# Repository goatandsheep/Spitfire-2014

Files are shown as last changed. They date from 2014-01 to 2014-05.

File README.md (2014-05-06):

McMaster Solar Car Club
=======================

Welcome to McMaster University's Solar Car Club's GitHub Repository. This is where we will keep all of our project files. We are currently in the process of transferring files from the Dropbox folder to here.

This is the link to the Solar Car Room Drawer Inventory: http://goo.gl/nMddYb

This is the link to the main Solar Car website: http://www.macsolarcar.com/

If you are new to GitHub, don't fret-we have included a tutorial on how to use it: http://goo.gl/4RcD2u

Note: [.md](https://en.wikipedia.org/wiki/Markdown) files can be opened like .txt files, but look cool up on GitHub

Target Release date: End of February, 2014

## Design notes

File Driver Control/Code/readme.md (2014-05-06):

TRI86 EV driver controls MSP430 firmware README
================================================

* This firmware is written to use the GNU GCC3 toolchain, please read the install instructions below.
* Refer to the board schematics, available on the Tritium website, for pinouts and device functionality.
* The firmware is licenced using the BSD licence.  There is no obligation to publish modifications.
* If you've written something cool and would like to share, please let us know about it!
* Contact James Kennedy with any questions or comments: [james@tritium.com.au](mailto:james@tritium.com.au)

Toolchain walkthrough (Windows MSPGCC instructions)
---------------------------------------------------

1. Download and [install the 2008-12-30 release of MSPGCC3](
  http://sourceforge.net/projects/mspgcc/files/Outdated/mspgcc-win32/snapshots/mspgcc-20081230.exe/download)
  The Tritium bootloader tool requires this specific version of GCC, as it has not yet been updated to use the
  output from the current GCC4 tools.

2. Download and install the [current MinGW](http://sourceforge.net/projects/mingw/files/), and use the install options for the C compliler + MSYS. This gets you `make`, `rm`, etc 

3. Set your path (system -> advanced -> environment variables -> path -> edit or similar) to include the three things above:
    1. `c:\mspgcc\bin`
    2. `c:\MinGW\bin`
    3. `c:\MinGW\msys\1.0\bin`
    4. or whatever path you installed them to.

4. Open a cmd prompt window, change to the directory with the firmware files, and type: make
  This should compile everything and produce an `.a43` and `.elf` file ouput

5. Still at the command line, type: `encrypt`. This should take the `.a43` and encryption key and produce a Tritium bootloader `.tsf` file targetted at the driver controls hardware. You may need to adjust the version number in the encrypt.bat file to match your driver controls hardware version number

6. Use the triFwLoad tool from the Tritium website, with a CAN base address of `0x500`, to bootload the `.tsf` file into the driver controls over the CAN bus

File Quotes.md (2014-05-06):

Funny Quotes
============

1. We've recently received a pedal, but nothing that can be described as a throttle.
2. Do we need brakes?
3. Why would you be braking with the turn signal on?
4. The circuit says 3.3V. Is it bad that I connected 5?
5. Did you check the baud rate?

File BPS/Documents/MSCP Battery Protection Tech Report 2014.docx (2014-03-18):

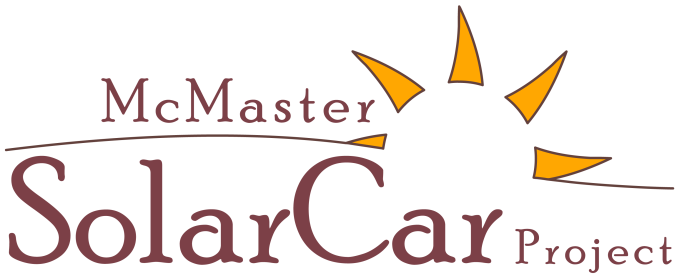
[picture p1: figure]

Battery Protection Tech Report
American Solar Challenge 2014
November 15, 2013

Compiled by:

Name | Title | E-mail
Michael Bot | Electrical Co-Manager | botmr@mcmaster.ca
Mhamad Salih Andy Li | Electrical Co-Manager Electrical Co-Manager | salihm@mcmaster.ca liy92@mcmaster.ca

McMaster Solar Car Project

McMaster University

Hamilton, Ontario, Canada

solarcar@mcmaster.ca

(905) 525-9140 ext. 27388

www.macsolarcar.com

Table of Contents

# 1 Introduction

The following report reviews the planned battery protection system (BPS) to be employed in the McMaster Solar Car Project’s (MSCP) entry into ASC2014.

A lithium polymer (LiPo) battery pack will be used in our ASC2014 entry. As such, the battery pack will employ fully active protection for over-voltage, under-voltage, over-temperature, and over-current conditions. Voltage and temperature measurements are taken down to the module level while a single current measurement is taken in series with the positive terminal of the battery pack. The measurements are digitized and monitored by a microcontroller.

In series with the battery pack positive terminal is a normally-open, non-latching contactor. If a measurement outside of the allowed limits is detected, a fault condition is recorded. Under a fault condition, the battery protection microcontroller removes the power supply to this contactor, electrically isolating the battery pack from the rest of the car. The protection system and disconnect contactor are installed within the battery enclosure such that the battery pack connector terminal is electrically isolated from the pack when the vehicle is switched off and the enclosure is removed for impound. In addition to the active protection elements listed above, a 100A fuse is also installed in series with the positive terminal as an added passive protection device.

As the battery protection system is still in development, some details have yet to be finalized and specifications may change. Should any major changes in design occur, we will notify ASC organizers as soon as possible. If any details are unclear we would be happy to answer any questions that the reviewers may have.

# 2 Battery Pack Specifications

The main battery pack will be constructed of 52 Southtop model 9989182 LiPo cells; the relevant specifications are identified below in Table 1. In race configuration, two cells are placed in parallel per module and 26 modules are placed in series. Since two cells are placed in parallel per module, the current limits for the battery pack are twice that of a single cell.

Table 1: South Top 9989182 LiPo Specifications

Item | Specifications | Comments
Nominal voltage | 3.70 V
Charge cut-off voltage | 4.20 V
Discharge cut-off voltage | 2.75 V
Nominal capacity | 20.000 Ah ± 5% (74 Wh) | 0.2C discharge rate (4 A)
Discharge current | Standard: 4 A Maximum: 40 A | Allowable temperature range: -20°C - 60°C
Charge current | Standard: 4 A Maximum: 20 A | Allowable temperature range: 0°C - 45°C
Maximum cell mass | 375 g
Cell cost | US $35.00

# 3 System Methodology

## 3.1 Protection System Set Points

From Table 1, the relevant battery protection system set-points were identified, along with the required actions of the battery protection system:

- Over-voltage
  - 4.10 V: if any module voltage exceeds 4.10 V, the battery pack is nearly fully charged. A warning is given to the driver via an indicator lamp and to the support crew over telemetry.
  - 4.20 V: if any module voltage exceeds 4.20 V, the battery pack is automatically electrically isolated from the vehicle and all measurement circuitry is disconnected.
- Under-voltage
  - 3.20 V: if any module voltage drops below 3.20 V, the battery pack is nearly discharged. A warning is given to the driver via an indicator lamp and to the support crew over telemetry.
  - 2.75 V: if any module voltage drops below 2.75 V, the battery pack is automatically electrically isolated from the vehicle and all measurement circuitry is disconnected.
- Over-current
  - 80 A (discharging): if the series discharging current exceeds 80 A, the battery pack is automatically electrically isolated from the vehicle and all measurement circuitry is disconnected.
  - 40 A (charging): if the series charging current exceeds 40 A, the battery pack is automatically electrically isolated from the vehicle and all measurement circuitry is disconnected.
- Over-temperature:
  - 45°C (charging): if a cell exceeds this temperature, discharging of the pack is still allowed but charging is not. A warning is given to the driver via an indicator lamp and to the support crew over telemetry. The charging over-current limit is lowered to 0 A until the cell temperatures drop below 45°C.
  - 60°C (discharging): if a cell exceeds this temperature, the battery pack is automatically electrically isolated from the vehicle and all measurement circuitry is disconnected.

## 3.2 Battery Protection System Design

### 3.2.1 System Overview

A block diagram of the battery protection system is shown in Figure 1. Note that only four battery modules are shown for clarity. In this arrangement, the measurement hardware of the BPS consists of three constituent parts: module mounted circuitry to locally measure voltage and temperature (battery side monitors), a current transducer circuit, and a central processor. Isolation of the battery pack is achieved using a normally open, non-latching contactor (Kilovac EV200AAANA).

The module temperatures and voltages are locally digitized by a DS2764 battery monitor IC and the current transducer outputs an analog voltage proportional to the battery pack current. The central processor sequentially polls each battery side monitor and measures the signal from the current transducer. Should a measurement outside of the ranges identified in section 3.1 be found, the corresponding action is taken. This approach is based largely on that used successfully by the MSCP for their 2009 World Solar Challenge entry. Currently, there are no plans to implement charge balancing or battery management into the system.

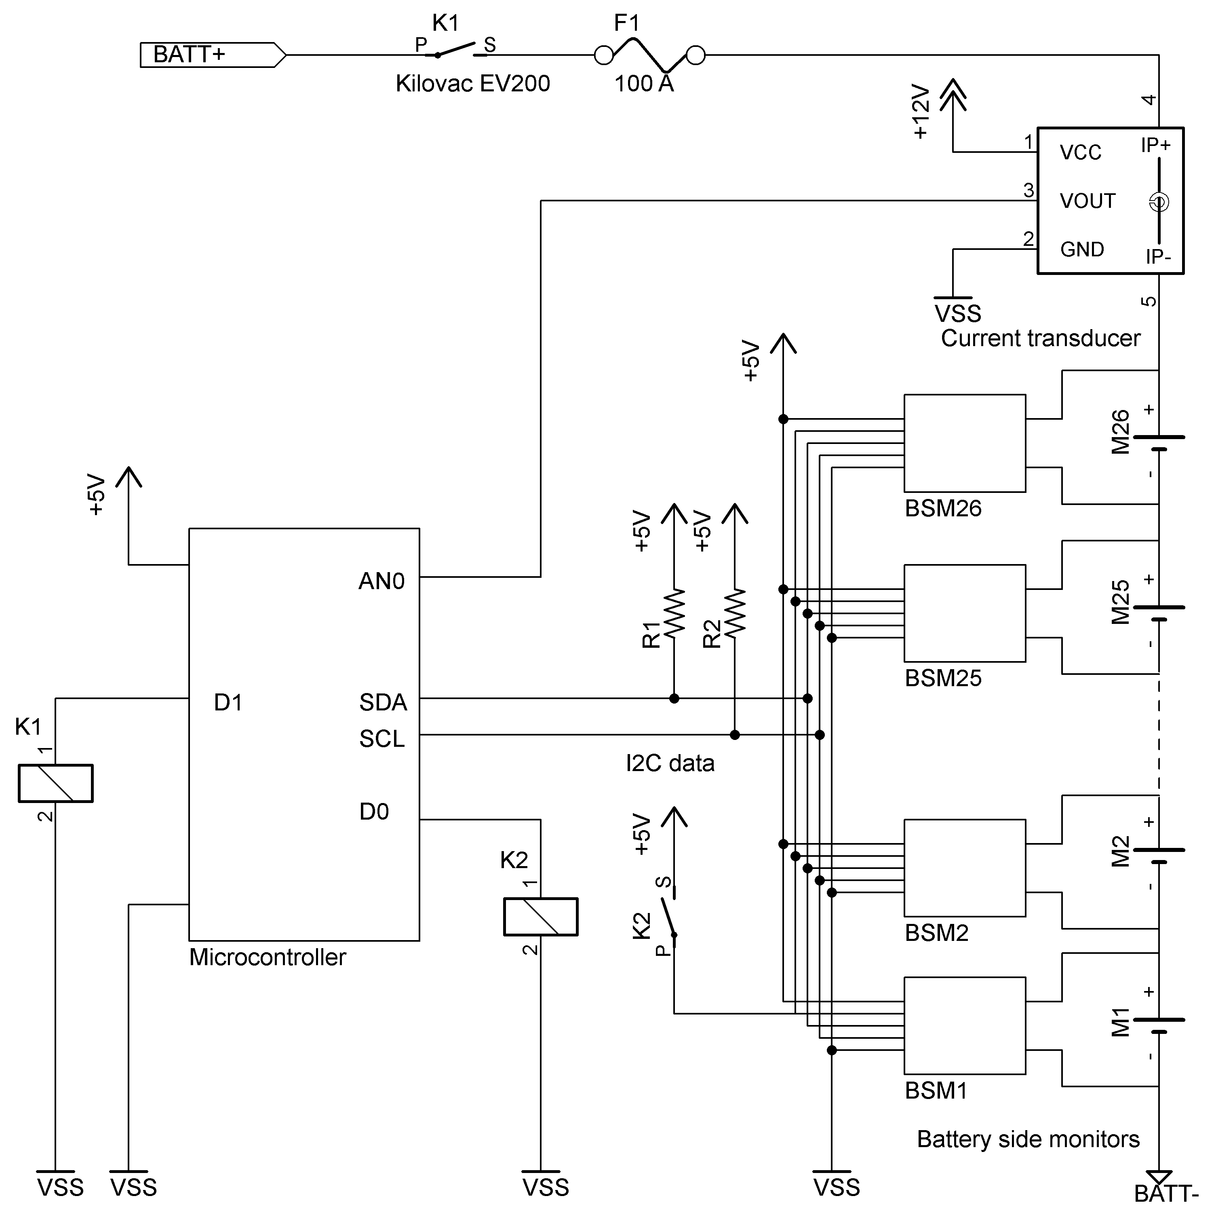
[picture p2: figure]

Figure 1: Block diagram of battery protection system

### 3.2.2 Battery Side Monitor

A schematic of the battery side monitor circuit is shown below in Figure 2. Each module in the battery pack will have a corresponding battery side monitor circuit; since there are 26 battery modules, the BPS will feature 26 battery side monitors.

The DS2764 battery monitor IC from Dallas Semiconductor was selected to provide voltage and temperature measurements. This sensor is designed to be powered by and monitor a single Li-ion cell; during operation, temperature and voltages are measured, digitized, and made available on an I²C digital bus. Module voltage is measured with 4.88 mV precision and is updated every 3.4 ms while temperature is measured with 0.125°C precision and is updated every 220 ms.

In order to provide ground isolation between each module and the data bus, an Analog Devices ADUM1251 I²C isolator was selected. This device is compatible with the voltage range of Li-ion cells and features bi-directional communication on the I²C data-line; this feature is vital since the central microcontroller has to send commands and receive data on the same wire.

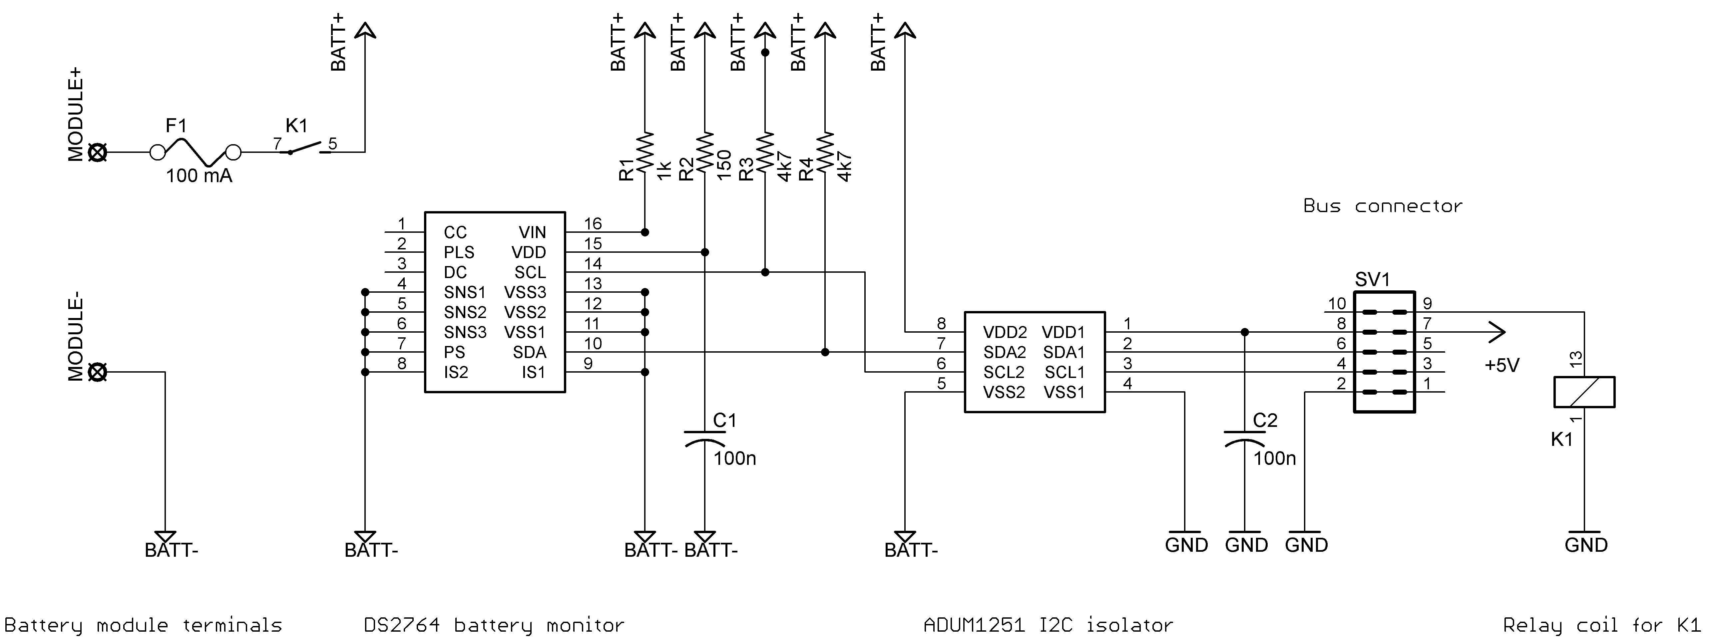
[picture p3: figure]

Figure 2: Schematic of battery side monitor circuit

The DS2764 monitor IC and the ADUM1251 I²C isolator IC receive some power directly from its battery module; together they draw approximately 2 – 3 mA through this connection. Therefore, provision is provided to isolate these loads when the BPS is offline or the set-points are exceeded. A Coto 9007-05-40 reed relay (1 Form A: SPST, normally open, non-latching) is used to accomplish this and is indicated by K1 in Figure 2. During normal operation, the central processor circuitry will energize the coils of each relay to connect the battery side circuitry to the module. When the BPS is powered off these relays will open, fully isolating the battery side monitor circuitry from the module.

The battery side monitor circuits will be attached to each module using hot-melt adhesive. The temperature sensor is located internally to the DS2764 IC. As such, when installed the IC case will placed in direct contact with the battery module casing. The battery side monitors are then daisy-chained to the central processor using a 10-pin ribbon cable and 2x5 IDC connectors.

### 3.2.3 Current Transducer

A LEM LA-50P closed-loop hall-effect type current transducer will be employed to measure current draw. This sensor is capable of bidirectional current measurement in the range of ±80 A. The closed-loop design allows non-contact measurements, providing galvanic isolation between the current measurement and the sensor output. To avoid accidental connection of high voltages to the central processor circuit, the current transducer will be located on a separate circuit board remote to the central processor.

The LA-50P sensor outputs a small bi-polar current proportional to the current through the sensor at a ratio of 1/2000. This output current will be converted to a voltage via a measurement resistor. An op-amp circuit will be used to scale and level-shift this signal to a voltage in the 0 – 5 V range required by the analog-to-digital converter on the central processor.

### 3.2.4 Central Processor

The central processor will consist largely of a PIC18F26K80 microcontroller. This microcontroller features 12-bit analog-to-digital conversion to ensure adequate measurement resolution from the current transducer.[^1] This device will continually poll the battery side monitors and current transducer and compare these measurements against the imposed set-points. Temperature measurements will be stored at 1°C precision while voltages will be stored at 4.88 mV precision.

Past experience with this microcontroller and a similar battery side monitor design has shown that this arrangement is capable of an entire system refresh rate of about 100 Hz. In order to prevent spurious readings from causing false disconnection of the battery pack from the car, the central processor will only take action after receiving ten consecutive readings outside of the imposed set-points. This reduces the effective refresh rate to approximately 10 Hz.

The central processor has two essential logic-level output signals: one to control power to the relays on each battery side monitor circuit (relay state or D0 in Figure 1) and one to control power to the main battery pack disconnect contactor (contactor state or D1 in Figure 1). These outputs are driven low under any fault conditions.

Under normal operation, the driver will momentarily power the BPS from the vehicle’s auxiliary battery. The central processor will assert relay state HIGH, causing each battery side monitor to be connected to its battery module. The central processor will then poll each sensor and the current transducer. If the system is found to be within safe limits, the central processor will assert contactor state HIGH, closing the battery pack contactor and connecting the battery pack to the car’s high voltage rail. This will cause the car’s 12 V rail (powered by a 96V to 12V DC/DC) to become live. At this point, the BPS will be powered by the 12 V rail and the auxiliary battery is disconnected.

Following the detection of a fault condition, the central processor drives both relay state and contactor state to logic low, causing disconnection of the battery side monitors from their modules and the battery pack from the high voltage rail of the car. Once a fault condition is asserted it can only be cleared by a hard reset of the BPS (ie – by powering down the solar vehicle and repeating the power-up procedure).

The logic level outputs of the microcontroller are capable of sinking 20 mA; therefore relay driver circuits are required to interface the logic outputs to the battery pack contactor and relays on the battery side monitors. This will be accomplished either using a logic-level relay stage, relay driver IC such as a NUD3112, or an n-MOSFET relay driver circuit.

### 3.2.5 Additional Outputs and Debugging Support

The battery protection microcontroller will feature additional outputs to help the race crew in debugging system errors and developing a race strategy. A 2x24 character LCD screen will be installed in the lid of the battery box and will display the last recorded fault condition (location and type of fault), maximum and minimum module voltages, maximum cell temperature, and measured hall-effect sensor current. A data link to the telemetry system will be employed and an additional RS232 debugging port (text output to a terminal) will be available. These communication links will be one-way only and cannot be used to change firmware settings on the BPS microcontroller.

# 4 Regulations Compliance and Scrutineering Demonstration

When constructed, provisions will be taken to ensure and demonstrate compliance with race regulations. In order to facilitate testing during scrutineering, additional battery side monitors identical to those installed in the battery pack will be provided for inspection. An additional connector on the BPS ribbon cable bus will also be provided. This will allow one of these spare sensors to be connected to the BPS in the place of one monitor installed on the battery pack. This spare monitor could then be connected to a power supply voltage reference and placed near a heating element for testing of the voltage and temperature set points.

In order to simulate overcurrent conditions, the microcontroller’s analog input will be disconnected from the current transducer circuitry and connected to test points to allow the injection of an analog voltage. Datasheets for the current transducer and associated circuitry will be provided along with pre-prepared calibration curves. These will be used to demonstrate the relationship between transducer current and analog voltage output.

During testing, the readings from the test points and the BPS status will be visible on the LCD screen attached to the BPS. Additionally, the state of any relays can be observed directly using an ohmmeter and by listening for their triggering.

Finally, the system set points will be rendered static following scrutineering. The set points will be hard-coded into the BPS firmware and cannot be changed without reprogramming the BPS microcontroller. This would only be possible through the replacement of the microcontroller or by accessing the programming pins in-circuit (on-board). As discussed in section 3.2.5, the only data connections accessible from outside the battery enclosure are one-way only (data transmitted from BPS). Once the battery enclosure lid is sealed following scrutineering, the only methods of modifying the BPS set points would firstly involve breaking the battery enclosure seal.

# 5 Concluding Remarks

This report has discussed the design approach taken for the battery protection system being built for use in the ASC2014 entry for the McMaster Solar Car Project. Intent was made to fully report all current information to indicate compliance with race regulations. Should any details appear unclear or contrary to the race rules, the McMaster Solar Car Project welcomes any questions or comments that the reviewers may have.

[^1] 12-bit precision corresponds to a resolution of 1.22 mV per division. If the current transducer output of ±80 A is scaled to 0 – 5 V, this corresponds to 31.25 mV/A, or approximately 26 mA per division

MSCP_BatteryProtectionTechReport_v05.docx i 11/14/2013

MSCP Battery Protection Tech Report 2014 i 11/14/2013

MSCP Battery Protection Tech Report 2014 6 11/14/2013

McMaster Solar Car Project: Battery Protection Tech Report

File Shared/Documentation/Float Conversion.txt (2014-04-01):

One of the challenges from this component was converting raw binary values into
floating point numbers. Not because this is difficult to do, but because PIC
floating point is not quite IEEE754 floating point.

Normally, you can convert raw binary into floating point with
    newFloat = *(float *)&oldInt;

But this is dependant on the floating point representation. After some testing,
we found raw values from a few floating point numbers:

 Int |  IEEE Float |  PIC Float
-----+-------------+-------------
 0.0 | 00 00 00 00 | 00 00 00 00
 1.0 | 3F 80 00 00 | 7F 00 00 00 
-1.0 | BF 80 00 00 | 7F 80 00 00
 2.0 | 40 00 00 00 | 80 00 00 00
-2.0 | C0 00 00 00 | 80 80 00 00
 0.5 | 3F 00 00 00 | 7E 00 00 00
-0.5 | BF 00 00 00 | 7E 80 00 00

IEEE Floating point representation:
 1 Sign bit
 8 Exponent bits
23 Fraction bits

Microchip Floating point representation:
 8 Exponent bits
 1 Sign bit
23 Fraction bits

Telemetry and Driver Display both receive data from the motor controller in raw
binary form of IEEE floating point. To convert to a useable Microchip floating
point format, the sign and exponent bits need to be shifted.

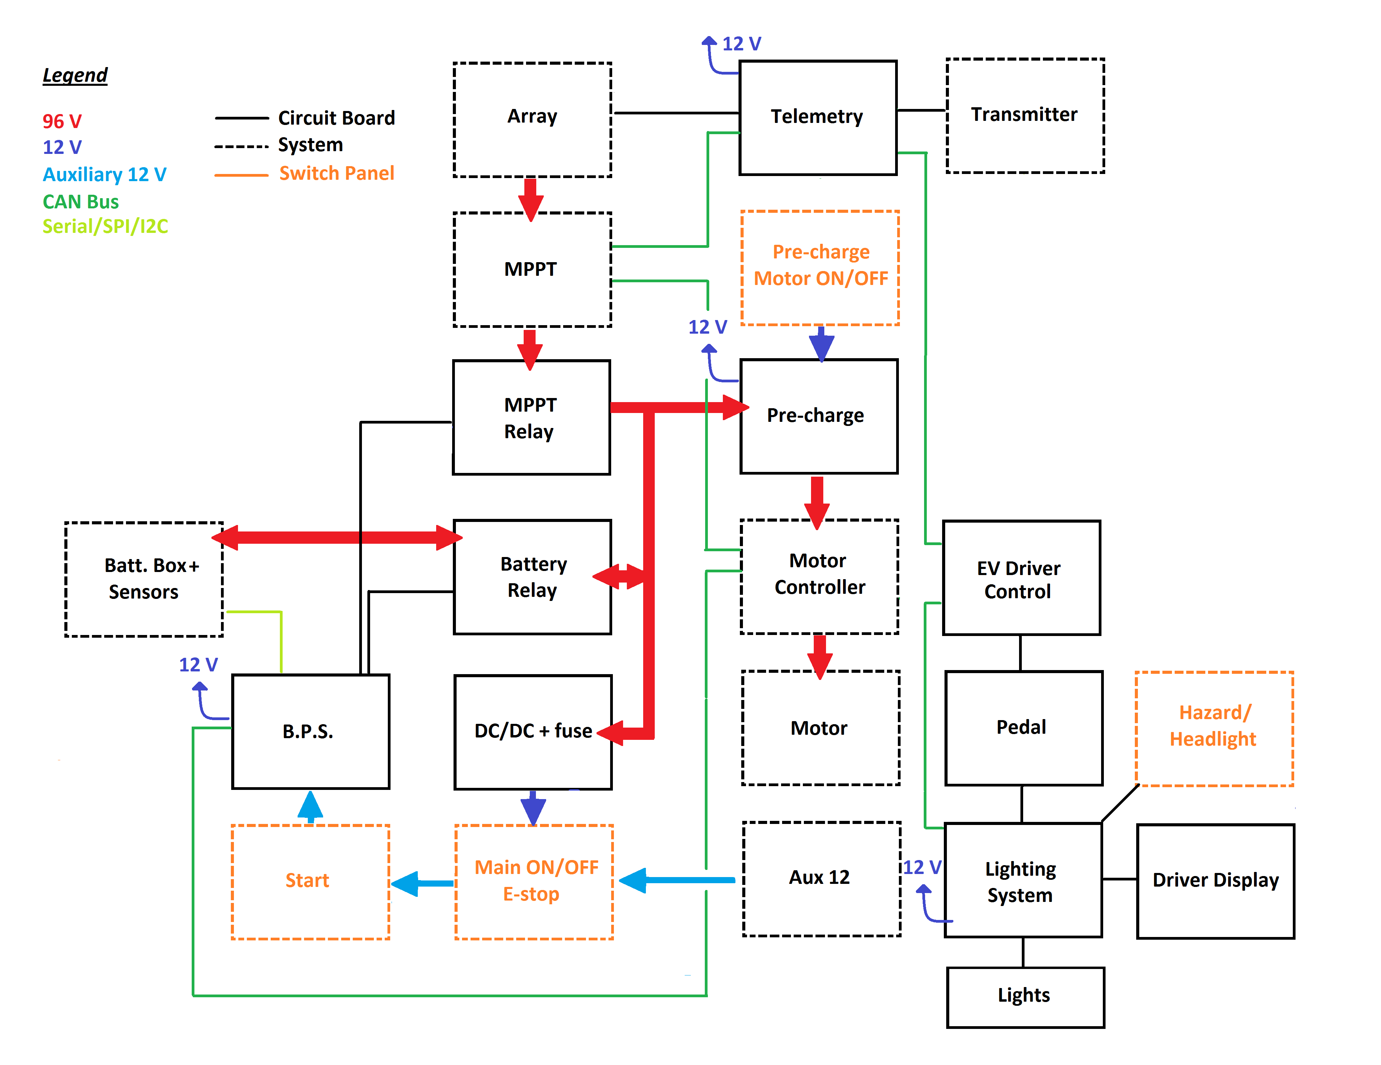
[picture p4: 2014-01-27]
Shared/Board Connections.png

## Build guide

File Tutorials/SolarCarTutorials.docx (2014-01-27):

Solar Car tutorials

The electrical tutorials offered by Solar Car are aimed toward beginners who are interested in electronics design. They will not teach you everything required to design practical electronic circuits, but will provide you with a fundamental understanding of the process of designing and building circuits and set you in the right direction. The tutorials will cover: electronic components, component selection and sampling, Soldering, Breadboard prototyping, design and simulation, Printed Circuit Board design and manufacturing, Control systems using an Arduino and a PIC microcontroller.

Note:

- Soldering tutorials are held at the solar car office (JHE B116) anytime an electrical manager is at the office, emails will be sent out.
- Only students who have soldered a working PicKit2 board will be able to practice control systems using a PIC microcontroller.
- PicKit2 Boards are used for debugging and programming microcontrollers
- There are a maximum of four (6) soldering irons at the solar car office, so you must sign up to let us know organize a schedule.
- Individuals who have never soldered before regularly take up to 4 hours to complete a PicKit2 board
- A PicKit2 board is sold (at cost – no profit) for $15, students get to keep the board they make
- Watch these videos before coming to the soldering tutorials:

http://www.youtube.com/watch?v=I_NU2ruzyc4

http://www.youtube.com/watch?v=3NN7UGWYmBY

Tuesday, September 17 (room and time TBD)

Components - basics

- RLC, package types, then using Falstad java app
- Voltage dividers, potentiometers
- Switches and relays
- Diodes and LEDs
- Breadboards, PCBs, DIP and SMD packages, resistor color codes
- Single Line diagrams, and conventional schematic layouts

Wednesday, September 18 (room and time TBD)

Components - moderate

- Chips:, 7 segment displays, LDO, ADC, 555 timer (using falstad)
- Microcontrollers, crystals, connectors
- Pull up and pull down resistors
- How to sample from TI, TE, Microchip

Tuesday, September 24 (room and time TBD)

Control systems Basics using an Arduino

- Downloading software
- I/O
- Blinking LED
- PWM
- Analog inputs
- Serial RX/TX

Wednesday, September 25 (room and time TBD)

Control systems Basics using an Arduino

- I2c using a temperature sensor
- SPI using an LED driver

Tuesday, October 1st (room and time TBD)

- Eagle CAD download
- Schematic design, shortcuts
- PCB Routing
- Shortcuts, rules, general standards (Bottom plane is GND, Top plane Power, etc)
- OSH park – manufacturing your PCBs

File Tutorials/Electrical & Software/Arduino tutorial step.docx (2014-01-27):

Output example

int LED = 11;

int t = 500;

void setup()

{

pinMode(LED, OUTPUT);

}

void loop()

{

digitalWrite(LED, HIGH);

delay(t);

digitalWrite(LED, LOW);

delay(10-t);

}

From here increase the frequency until PWM

Input example

int switchPin = 4;

int LED = 11;

boolean toggle = false;

void setup()

{

pinMode(switchPin, INPUT);

pinMode(LED, OUTPUT);

}

void loop()

{

if(digitalRead(switchPin) == HIGH)

{

delay(5);

toggle = !toggle;

}

while(digitalRead(switchPin) == HIGH){}

if(toggle == true)

{

digitalWrite(LED, HIGH);

}

else

{

digitalWrite(LED, LOW);

}

}

POT and serial example

int LED = 11;

int pot = 0;

void setup()

{

pinMode(LED, OUTPUT);

Serial.begin(9600);

}

void loop()

{

Serial.println(analogRead(pot));

analogWrite(11, map(analogRead(pot), 0, 1023, 0, 255));

delay(50);

}

I2C example with temperature sensor

#include <Wire.h>

int ID = 72;

void setup()

{

Serial.begin(9600);

Wire.begin();

}

void loop()

{

Wire.beginTransmission(ID);

Wire.write(0);

Wire.endTransmission();

Wire.requestFrom(ID, 1);

while(Wire.available() == 0);

float temp = Wire.read();

Serial.print(temp);

Serial.println(" degrees Celsius");

delay(100);

}

First SPI example

#include <SPI.h>

int LE = 10;

int OE = 9;

int data = 0b00001111;

void setup()

{

pinMode(LE, OUTPUT);

pinMode(OE, OUTPUT);

SPI.begin();

}

void loop()

{

digitalWrite(OE, HIGH);

digitalWrite(LE, HIGH);

SPI.transfer(data);

digitalWrite(LE, HIGH);

digitalWrite(LE, LOW);

digitalWrite(OE, LOW);

delay(200);

}

Final example with POT and SPI

#include <SPI.h>

int LE = 10;

int OE = 9;

int pot = 0;

int value;

int binvalue;

int data[] = {0b00000000, 0b10000000, 0b11000000, 0b11100000, 0b11110000};

void setup()

{

pinMode(LE, OUTPUT);

pinMode(OE, OUTPUT);

SPI.begin();

}

void loop()

{

value = analogRead(pot);

binvalue = map(value, 0, 1023, 0, 5);

digitalWrite(OE, HIGH);

digitalWrite(LE, HIGH);

SPI.transfer(data[binvalue]);

digitalWrite(LE, HIGH);

digitalWrite(LE, LOW);

digitalWrite(OE, LOW);

}

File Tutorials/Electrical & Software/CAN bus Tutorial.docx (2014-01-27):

CAN Bus Tutorial

Introduction to Controller Area Network

http://www.youtube.com/watch?v=sw3ADKPo1Uo

http://www.youtube.com/watch?v=RlZGwP0WyFY

Texas Instruments’ detailed CANbus architecture (read sections 1 up to 5, excluding 5.1+)

http://www.ti.com/lit/an/sloa101a/sloa101a.pdf

Watch all 4 parts of the following video series:

http://www.youtube.com/watch?v=m8HTVlEC7Lg

DigiKey’s take on CANbus video (watch this then attempt the next link, your goal is to understand it, not finish it):

http://www.youtube.com/watch?v=6KQylhGLvHo

Digikey’s CAN bus tutorial:

http://dkc1.digikey.com/us/en/tod/Renesas/CANBasicsPart-1_NoAudio/CANBasicsPart-1_NoAudio.html

You are now an expert in CAN bus theory!

CAN Bus Hardware general layout:

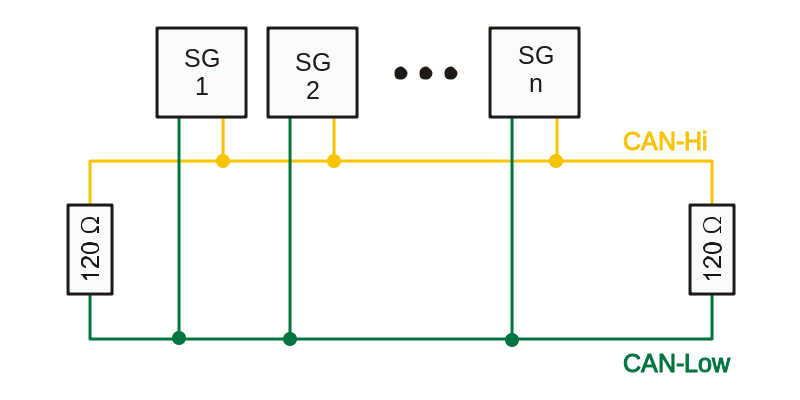
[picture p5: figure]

- Where SG1, SG2… SGn are the nodes attached on the Bus lines (CAN-HIGH and CAN-LOW)
- 120 Ohm termination resistors are used at the ends of the bus for minimizing reflections

Hardware Design (EagleCAD schematic)

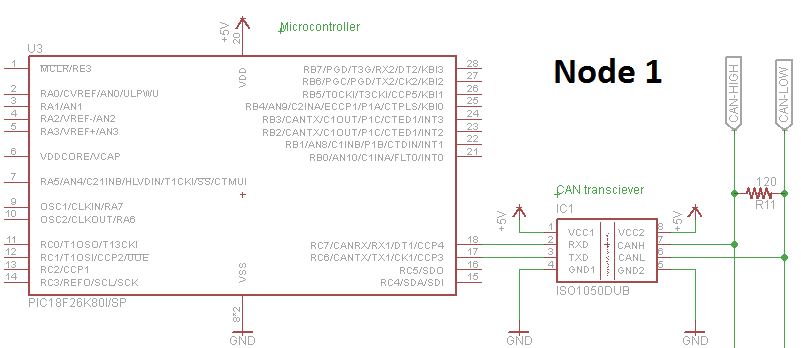
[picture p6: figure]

- This is the typical CAN bus hardware design we use in the solar car circuits
- We use the pic18f26k80 simply for reducing chip usage and space (the 26k80 has its own built in CAN interface, which directly connects to the CAN transceiver: Texas Instruments’ ISO1050 isolated 5V CAN transceivers, and these are sample-able aka we get them for free)
- If you don’t use the microcontrollers that have built in CAN interfacing (for CAN bus required circuits), then you would have to use SPI to communicate to a separate CAN interface chip (MCP2515 CAN interface chip), then the interface chip connects to the transceiver, which then connects to the Bus (CANH and CANL). Basically “Microcontroller → MCP2515 → ISO1050 → Bus” instead of “Microcontroller → ISO1050 → Bus”. In total, you are wasting 4 pins on the microcontroller (SPI requires SDI, SDO, SCL, SS) and space for the CAN interface chip. Remember, surface area = money in circuit design world, so minimizing is ideal. So make sure you use the 26k80 MCU if your circuit requires CAN bus.
- For the actual bus itself, we use a CAT5-B type wire and two RJ-45 connectors on each board. Two connectors are required because all the boards are daisy-chained.
- Make sure to include a ¼ W 120 Ohm termination resistor for all the boards in the schematic and Board files. Do not solder the resistors on the boards. This will be decided once all the boards are installed into spitfire and the first/last boards are chosen based on minimizing cat5 wiring.
- The CAT5 wires will contain the following (in order): 12V(1), 5V(2), GND(3), CANH(1), CANL(1). The 12V will be accessed by the MPPTs and the Motor controller, the rest of the nodes will access the 5V line.

CAN Bus system (simple example)

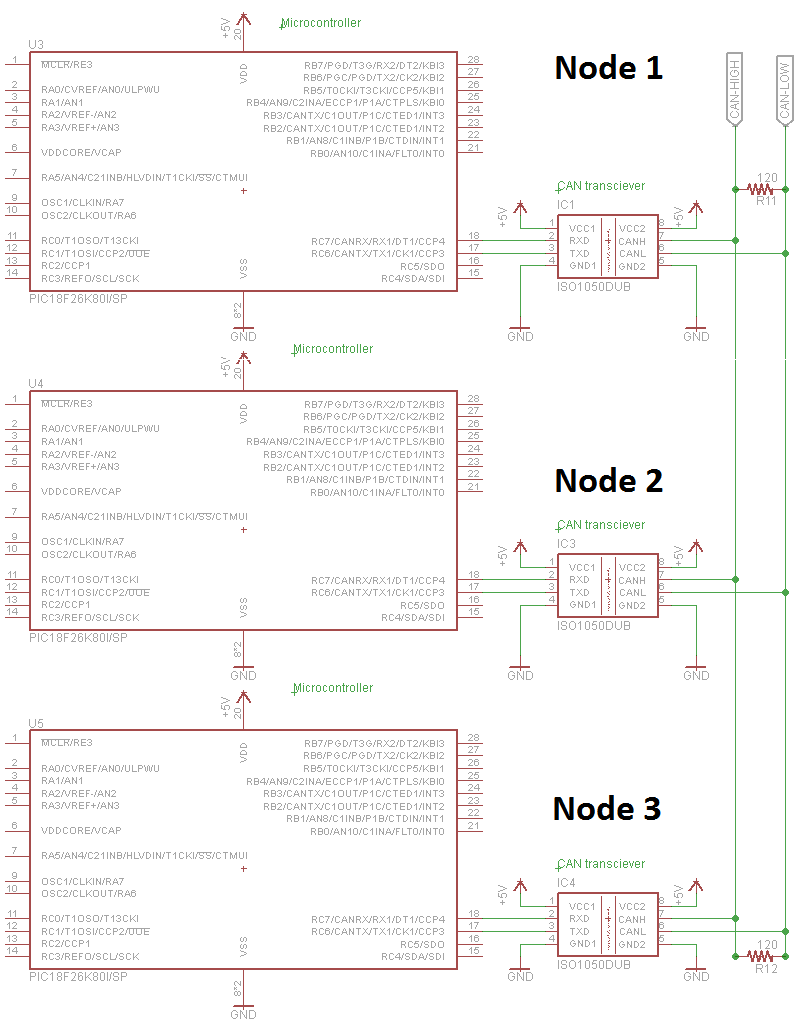
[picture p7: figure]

CAN bus software implementation (accessible from n002.c in Dropbox\Battery Protection Share\CCS\n002.c)

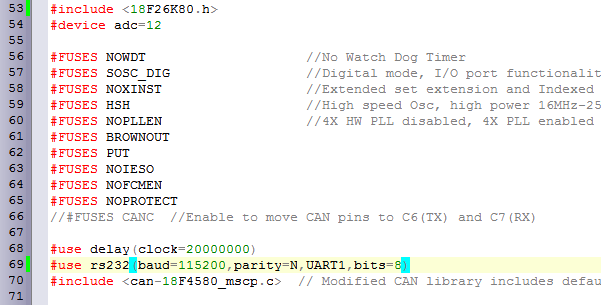
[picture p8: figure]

- In the beginning of the code, make sure to include the header files for the MCU you are using, for this example we are using the 18f26k80 microcontroller
- The #FUSES are already included when creating a new source file
- CAN bus requires high frequency operation, all CAN bus circuits require a minimum of a 20 MHz external clock, make sure to include it in the #use delay(clock=…)
- The <can-18F4580_mscp.c> is a modified can library which contains timing settings that match the drivetek V3 MPPTs we are using in Spitfire
- This is a timer interrupt initialization for counting milliseconds

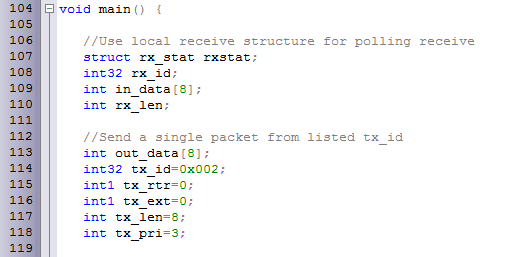
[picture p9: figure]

- Rx_stat, id, data and length are all the frames which are received by this specific node from the CAN bus, hence why their values are not specified
- Out_data = output data, each element of this array is a single byte for a total of 8 bytes
- Tx_id is the transmitting ID, in other words this is the ID number of this specific node. The Lower the ID number, the higher priority for that specific node. So when programming your circuits, assign reasonable ID numbers to maintain message priority for boards such as motor controller, BPS and MPPTs

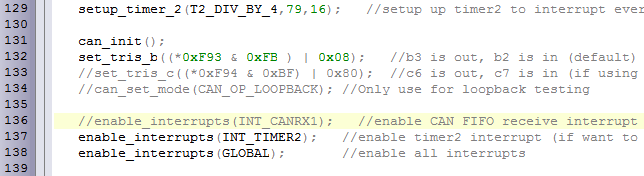
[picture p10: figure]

- Setup timer starts the timer interrupt which we had prepared to count milliseconds earlier
- Can_init(); starts the CAN module
- Set_tris_b sets the CAN Rx and Tx for receiving and transmitting on the specified CAN pins of the microcontroller
- Then enable interupts

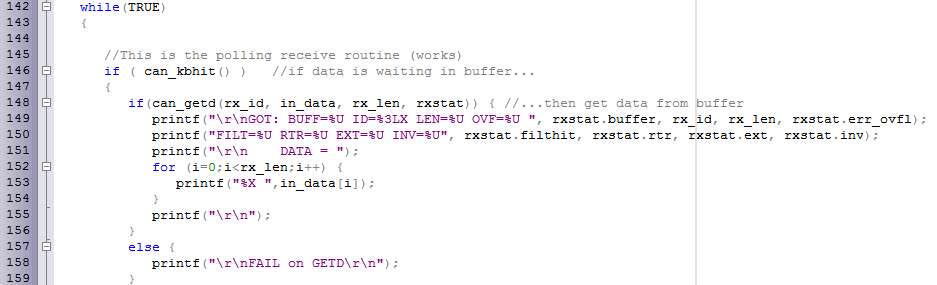
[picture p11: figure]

- Now during every cycle of the microcontroller, you want to check the BUS for information, this is done by can_kbhit() which checks for data in the buffer
- If data is waiting in the buffer, then access it using the function can_getd, and assign the data to the following fields: rx_id, in_data, rx_len, rxstat
- In this example, the data is printed out to the screen, for the purpose of your circuits, you must check which node did this data come from by using a lookup table that compares the ID number to the ID numbers that you are interested in. for example: lets say Motor controller has an ID = 4, and you are coding the Driver display which needs to access the RPM, then you would check if the data received is from ID = 4, from there you would access in_data and process the information to display it to the driver display circuit

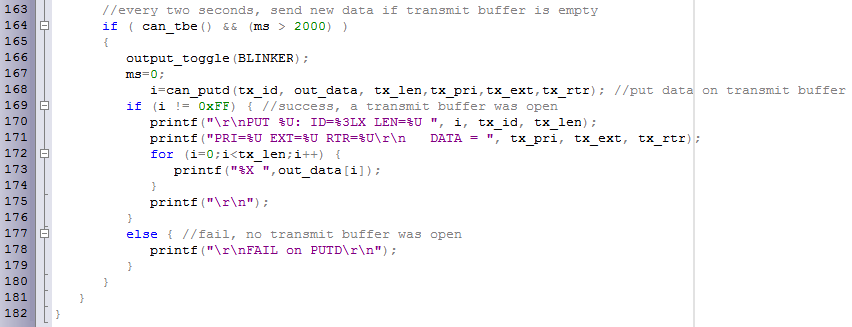
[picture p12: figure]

- Can_tbe() checks if the transmit buffer is empty
- This if statement checks if the timer interrupt has passed the 2 second mark AND if the transmit buffer is empty prior to proceeding
- If both transmit buffer is empty and timer > 2 seconds, then you can load data to the transmit buffer using can_putd() with the input arguments representing the ID number, 8 bytes of data, length… etc
- The function can_putd returns 0xFF during a fail, so !0xFF = returned success, for this example it prints out the transmitted frames during a success, for your circuits, you won’t need to print anything, but rather send valuable information (depending on what your circuit does)

I hope this has been a good walkthrough of setting up CAN bus. If anything is not clear, please ask me questions as I am happy to help, point out if any part is confusing and I will try to make it more straightforward.

Mhamad Salih

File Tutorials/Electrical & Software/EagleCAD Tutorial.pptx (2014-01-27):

## EagleCAD Tutorial

Andy Li
McMaster Solar Car Project

## What is Eagle?

- Stands for Easily Applicable Graphical Layout Editor
- Draw out circuit schematics
- Design circuit boards
- Routing a good board takes patience and practice

## Project examples

## Terminology

- Routes connect the circuit together (wires)
- Pads are what the parts are soldered to
- Default route thickness is 0.016in, good enough for most connections
- Use thicker routes for high voltage/current
- PCBs sometimes have more than one layer, use vias when routing to connect multiple layers

## Terminology (cont.)

- Ratsnest is a function that cleans up connections on the board
- Ground plane represents ground, traces are cut out of the ground plane
- Surface mount vs through hole packages
- Eagle recognises a LOT of different components, organized by libraries
- Finished PCBs are either milled out of copper board, or made professionally

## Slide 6

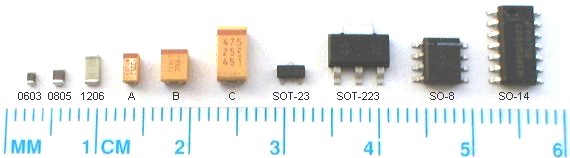
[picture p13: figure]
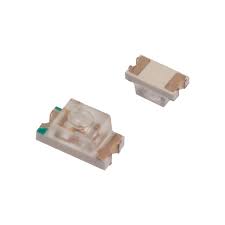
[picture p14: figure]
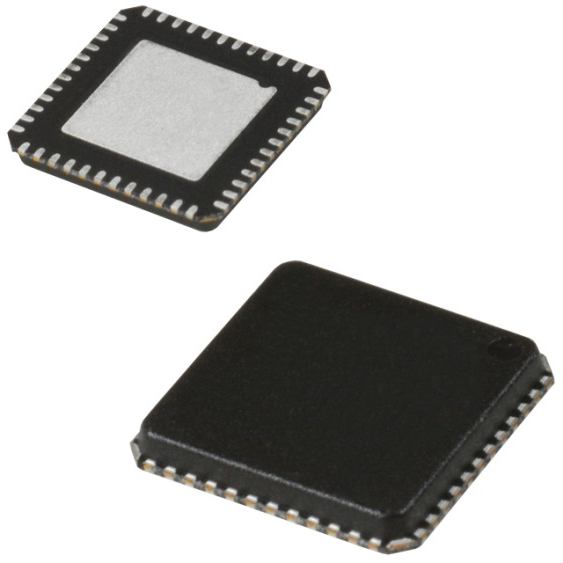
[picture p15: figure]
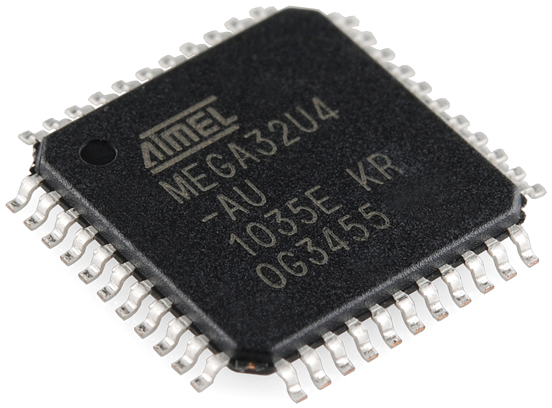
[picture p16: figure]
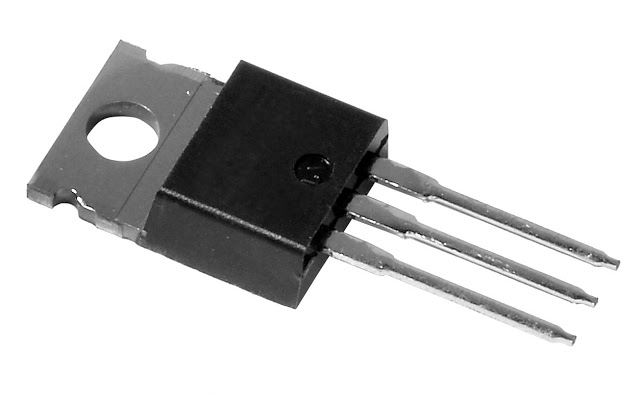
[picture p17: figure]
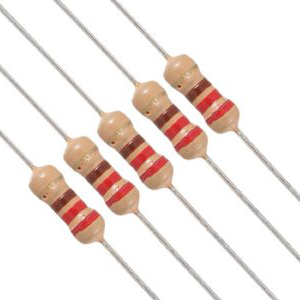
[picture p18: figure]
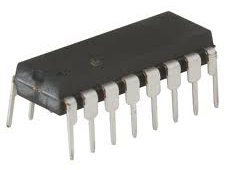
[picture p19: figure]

## Designing a circuit

- Start with the largest component in the circuit (microcontroller, chip, etc)
- Arrange components into groups (power supply, filters, serial interface, etc)
- Keep the schematic as tidy as possible, spread your components out a little, avoid cluttering wires
- Label important nodes (supply, ground, output, I2C/SPI lines, etc)

## Routing a board

- Start with the largest component in the circuit
- Place components where there would be the least overlap
- Once everything is arranged neatly, create a ground plane, and start routing the board group by group, beginning with the closest components
- Take into account spacing between routes and components

## Example: Op-Amp Circuit

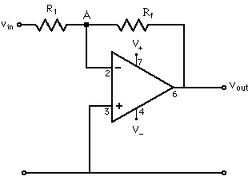
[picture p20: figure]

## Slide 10

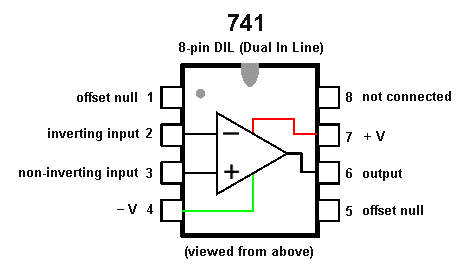
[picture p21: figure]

## Exercise: 555 Timer circuit

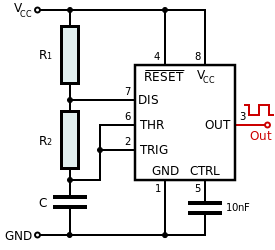
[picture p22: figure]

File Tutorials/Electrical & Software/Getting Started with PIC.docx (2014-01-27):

# PIC Tutorial

For more information, refer to the CCS internal help or the CCS S manual stored at D:\Documents\Dropbox\MSCP-elec share\Manuals (“MSCP-elec share” may be referred to as “Battery Protection Share” for some people).

1. Download/install MPLab IDE 8.8 from http://www.microchip.com/stellent/idcplg?IdcService=SS_GET_PAGE&nodeId=1406&dDocName=en019469
2. Copy over the CCS folder from the solarcar server. If you are at home you may need to VPN into the McMaster network (instructions at http://www.mcmaster.ca/uts/network/vpn/)
- CCS folder is at \\pc-solarcar.eng.mcmaster.ca\Files\Software\CCS PCWHD v4.120
3. Installing CCS
- run pcwhdupd.exe
- it will ask for registration files. Don’t give any registration files and complete the installation
- run the keygen (in the CCS folder) and place files in the main part of the PIC C folder (C: -> program files (x86) -> PICC, unless you put it somewhere else). The keygen produces the registration files and keeping them in the PICC folder will enable them.
- run ideutilsupd.exe (in CCS folder)
- download and install the MPLab plug-in for CCS found here: http://www.ccsinfo.com/downloads.php
- to check if everything worked correctly:
- open CCS and attempt to create a new project using the PIC wizard.
- If your registration files (.crg) are no good you will not be able to select any PICs from the dropdown list. You can fix this by copying the .crg’s from \\pc-solarcar.eng.mcmaster.ca\Files\Software\CCS PCWHD v4.120\example crg into your PICC folder. You may need to restart CCS to complete the fix
4. Creating a new project
  - Open CCS (shortcut is called “PIC C Compiler”). From the “Project” menu or ribbon, click on “PIC Wizard”. It will ask you where you want to save your new project. Making a new folder for it is suggested as the compiler will create a lot of files.
  - If you want the project to be accessible to other team members, locate the new folder in D:\Documents\Dropbox\MSCP-elec share\CCS (“MSCP-elec share” may be referred to as “Battery Protection Share” for some people)
  - The PIC Wizard will now open and you will be presented with the “General” tab. The box on the left side of the wizard allows you to select between several tabs. In order to get a basic blinker working, you will only need the “General” tab and possibly the “Intr Oscillator Config” tab. The others are described here if you’re interested.
    i. General: Here you can select your PIC (e.g. PIC16F883) and set your oscillator frequency (most common are 20 MHz external crystal or 8 MHz internal RC). Remember to select the oscillator you are using from the drop-down menu. If you are given the option to disable the watchdog timer, you should do this here as well.
    ii. Examples: This should create for you a basic LED blinker code on a pin that you select. Disclaimer: may not work.
    iii. Analog: Used to set up analog inputs (use your PIC for measuring voltages). Select which pins you want enabled as analog inputs. If your PIC has a 10-bit ADC (most), use ”Units: 0-1023”; if it is 12-bit use “Units: 0-4095”.
    iv. Communications: Used to set up some types of digital communication including RS232 (aka UART or serial port) and I2C. RS232 is often used for communicating with a PC, while I2C is used for communicating with other chips.
    v. SPI: Used to set up Serial Peripheral Interface, which is another type of digital communication. SPI can also be used to communicate with shift registers.
    vi. Drivers: Allows you to include libraries for interfacing with several other common chips (EEPROMs, real-time clocks, A/D converters etc.). Unless you are using one of the chips referenced in this tab, you can skip it.
    vii. Header files: Allows you to include standard C libraries (string.h, math.h, etc.). Note that complex math operations (square root, logarithm, trigonometry etc.) will be very slow on a PIC, as is floating point (decimal support).
    viii. High/low voltage: The PIC has a module called the HLVD (high/low-voltage detect) that is used to monitor the power supply voltage. This tab is used to enable and configure it.
    ix. Interrupts: An interrupt service routine (ISR) is a block of code that is triggered in response to some event (the interrupt). You can set up code that executes at a fixed time interval (timer interrupt) or when a button is pressed (external interrupt), for example. There are many other interrupts as well.
    x. Intr Oscillator Config: This tab allows you to enable the PIC’s internal oscillator and set its operating frequency. Used when you do not need the precise timing of an external crystal for a system clock.
    xi. I/O Pins: Allows you to define different pins as digital inputs or outputs. Usually skipped because the digital I/O routines in CCS will set the pin’s “direction” (input or output) as necessary when they are called.
    xii. Timers: Used to configure the PIC’s onboard counters. A counter is a simple module holding a number that increases its value by one at some fixed time interval. Used for timing external events, triggering periodic interrupts, and so on.
    xiii. PCH Timers: Allows configuration of an extra two counters only available on PIC18s.
    xiv. LCD (Internal): On PICs that have an onboard LCD segment driver, this tab is used to set it up. Does not apply to any PICs in current Solar Car use.
    xv. LCD (External): Allows you to include a driver for standard 14-pin LCDs (using a 7-pin interface). We generally use the flex_lcd.c driver instead.
    xvi. Capacitive Touch: Configuration for capacitive touchscreen interface module. Not tested by Solar Car yet.

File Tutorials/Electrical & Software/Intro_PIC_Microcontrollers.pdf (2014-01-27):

# An Introduction to PIC Microcontrollers

# SECTION I

# The PIC Microcontroller Family

The PIC microcontroller family is manufactured by Microchip Technology Inc. Currently they are one of the most popular microcontrollers, used in many commercial and industrial applications. Over 120 million devices are sold each year.

The PIC microcontroller architecture is based on a modifi ed Harvard RISC (Reduced Instruction Set Computer) instruction set with dual-bus architecture, providing fast and fl exible design with an easy migration path from only 6 pins to 80 pins, and from 384 bytes to 128 kbytes of program memory.

PIC microcontrollers are available with many different specifi cations depending on:

- Memory Type
– Flash
– OTP (One-time-programmable)
– ROM (Read-only-memory)
– ROMless
- Input–Output (I/O) Pin Count
– 4–18 pins
– 20–28 pins
– 32–44 pins
– 45 and above pins
- Memory Size
– 0.5–1 K
– 2–4 K
– 8–16 K
– 24–32 K
– 48–64 K
– 96–128 K
- Special Features
– CAN
– USB

www.newnespress.com

CHAPTER 1

– LCD
– Motor Control
– Radio Frequency

Although there are many models of PIC microcontrollers, the nice thing is that they are upward compatible with each other and a program developed for one model can very easily, in many cases with no modifi cations, be run on other models of the family. The basic assembler instruction set of PIC microcontrollers consists of only 33 instructions and most of the family members (except the newly developed devices) use the same instruction set. This is why a program developed for one model can run on another model with similar architecture without any changes.

All PIC microcontrollers offer the following features:

- RISC instruction set with only a handful of instructions to learn
- Digital I/O ports
- On-chip timer with 8-bit prescaler
- Power-on reset
- Watchdog timer
- Power-saving SLEEP mode
- High source and sink current
- Direct, indirect, and relative addressing modes
- External clock interface
- RAM data memory
- EPROM or Flash program memory

Some devices offer the following additional features:

- Analog input channels
- Analog comparators
- Additional timer circuits
- EEPROM data memory
- External and internal interrupts
- Internal oscillator

### 4 Chapter 1

- Pulse-width modulated (PWM) output
- USART serial interface

Some even more complex devices in the family offer the following additional features:

- CAN bus interface
- I²
C bus interface
- SPI bus interface
- Direct LCD interface
- USB interface
- Motor control

Although there are several hundred models of PIC microcontrollers, choosing a microcontroller for an application is not a diffi cult task and requires taking into account these factors:

- Number of I/O pins required
- Required peripherals (e.g., USART, USB)
- The minimum size of program memory
- The minimum size of RAM
- Whether or not EEPROM nonvolatile data memory is required
- Speed
- Physical size
- Cost

The important point to remember is that there could be many models that satisfy all of these requirements. You should always try to fi nd the model that satisfi es your minimum requirements and the one that does not offer more than you may need. For example, if you require a microcontroller with only 8 I/O pins and if there are two identical microcontrollers, one with 8 and the other one with 16 I/O pins, you should select the one with 8 I/O pins.

Although there are several hundred models of PIC microcontrollers, the family can be broken down into three main groups, which are:

- 12-bit instruction word (e.g., 12C5XX, 16C5X) (also referred to in this book as the 12 Series and the 16C5X Series)

The PIC Microcontroller Family 5

- 14-bit instruction word (e.g., 16F8X, 16F87X) (also referred to in this book as the 16 Series)
- 16-bit instruction word (e.g., 17C7XX, 18C2XX) (also referred to in this book as the 17 Series and the 18 Series).

All three groups share the same RISC architecture and the same instruction set, with a few additional instructions available for the 14-bit models, and many more instructions available for the 16-bit models. Instructions occupy only one word in memory, thus increasing the code effi ciency and reducing the required program memory. Instructions and data are transferred on separate buses, so the overall system performance is increased.

The features of some microcontrollers in each group are given in the following sections.

## 1.1 12-bit Instruction Word

Table 1.1 lists some of the devices in this group. These devices have a very simple architecture; however, as the prices of 14-bit devices have declined, it is rarely necessary to use a 12-bit device these days, except for the smaller physical size.

Table 1.1: Some 12-bit PIC Microcontrollers

Microcontroller | Program Memory | Data RAM | Max Speed (MHz) | I/O Ports | A/D Converter
12C508 | 512 12 | 25 | 4 | 6 | –
16C54 | 384 12 | 25 | 20 | 12 | –
16C57 | 2048 12 | 72 | 20 | 20 | –
16C505 | 1024 12 | 41 | 4 | 12 | –
16C58A | 2048 12 | 73 | 20 | 12 | –

PIC12C508: This is a low-cost, 8-pin device with 512 12 EPROM program memory, and 25 bytes of RAM data memory. The device can operate at up to 4-MHz clock input and the instruction set consists of only 33 instructions. The device features six I/O ports, 8-bit timer, power-on reset, watchdog timer, and internal 4-MHz oscillator capability. One of the major disadvantages of this microcontroller is that the program memory is EPROM-based and it cannot be erased or programmed using the standard programming devices. The program memory has to be erased using an EPROM eraser device (an ultraviolet light source).

The “F” version of this family (e.g., PIC12F508) is based on fl ash program memory, which can be erased and reprogrammed using the standard PIC programmer devices. Similarly, the “CE” version of the family (e.g., PIC12CE518) offers an additional 16-byte nonvolatile EEPROM data memory.

Figure 1.1 shows the pin confi guration of the PIC12F508 microcontroller.

### 6 Chapter 1

PIC16C5X: This is one of the earliest PIC microcontrollers. The device is 18-pin with a
384 12 EPROM program memory, 25 bytes of RAM data memory, 12 I/O ports, a timer, and a watchdog. Some other members in the family, such as PIC16C56, have the same architecture but more program memory (1024 12). PIC16C58A has more program memory (2048 12) and also more data memory (73 bytes of RAM). Figure 1.2 shows the pin confi guration of the PIC16C56 microcontroller.

PIC 12F508/509
1

2

3

4

VDD | VSS 8

7

6

5

GP5/OSC1/CLKIN | GP0/ICSPDAT
GP4/OSC2 | GP1/ICSPCLK
GP3/MCLR/VPP | GP2/T0CKI

Figure 1.1: PIC12F508 Microcontroller PIC16CR58 PIC16C58 PIC16CR56 PIC16C56 PIC16CR54 PIC16C54

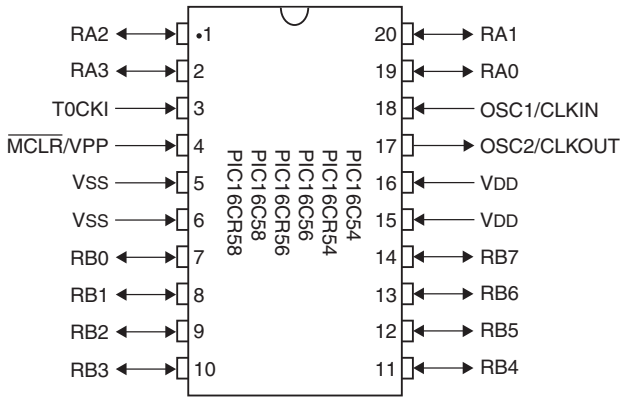
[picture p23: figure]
T0CKI; MCLR/VPP; VSS; OSC1/CLKIN; OSC2/CLKOUT; VDD

Figure 1.2: PIC16C56 Microcontroller

## 1.2 14-bit Instruction Word

This is a big family that includes many models of PIC microcontrollers. Most of the devices in this family can operate at up to a 20-MHz clock rate. The instruction set consists of 35 instructions. These devices offer advanced features such as internal and external interrupt sources. Table 1.2 lists some of the microcontrollers in this group.

PIC16C554: This microcontroller has similar architecture to the PIC16C54 but the instructions are 14 bits wide. The program memory is 512 14 and the data memory is 80 bytes of RAM. There are 13 I/O pins and each pin can source or sink 25 mA of current. Additionally, the device contains a timer and a watchdog.

The PIC Microcontroller Family 7

PIC16F84: This has been one of the most popular PIC microcontrollers for a very long time. This is an 18-pin device and it offers 1024 14 fl ash program memory, 36 bytes of data RAM, 64 bytes of nonvolatile EEPROM data memory, 13 I/O pins, a timer, a watchdog, and internal and external interrupt sources. The timer is 8 bits wide but can be programmed to generate internal interrupts for timing purposes. PIC16F84 can be operated from a crystal or a resonator for accurate timing. A resistor-capacitor can also be used as a timing device for applications where accurate timing is not required. Figure 1.3 shows the pin confi guration of this microcontroller. The pin descriptions are given in Table 1.3.

PIC16F877: This microcontroller is a 40-pin device and is one of the popular microcontrollers used in complex applications. The device offers 8192 14 fl ash program memory,

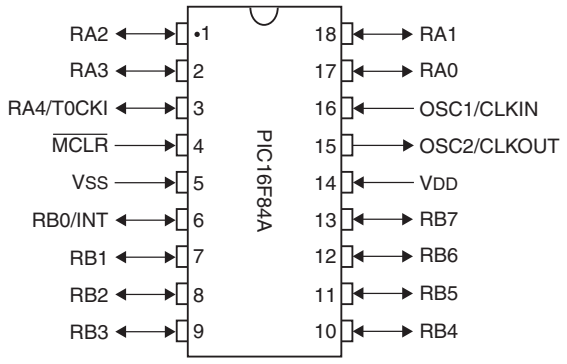
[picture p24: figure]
RA4/T0CKI; MCLR; VSS; RB0/INT; OSC1/CLKIN; OSC2/CLKOUT; VDD; PIC16F84A

Figure 1.3: PIC16F84 Microcontroller Pin Confi guration

Microcontroller | Program Memory | Data RAM | Max Speed (MHz) | I/O Ports | A/D Converter
16C554 | 512 14 | 80 | 20 | 13 | –
16C64 | 2048 14 | 128 | 20 | 33 | –
16F84 | 1024 14 | 36 | 10 | 13 | –
16F627 | 1024 14 | 224 | 20 | 16 | –
16F628 | 2048 14 | 224 | 20 | 16 | –
16F676 | 1024 14 | 64 | 20 | 12 | 8
16F73 | 4096 14 | 192 | 20 | 22 | 5
16F876 | 8192 14 | 368 | 20 | 22 | 5
16F877 | 8192 14 | 368 | 20 | 33 | 8

Table 1.2: Some 14-bit Microcontrollers

### 8 Chapter 1

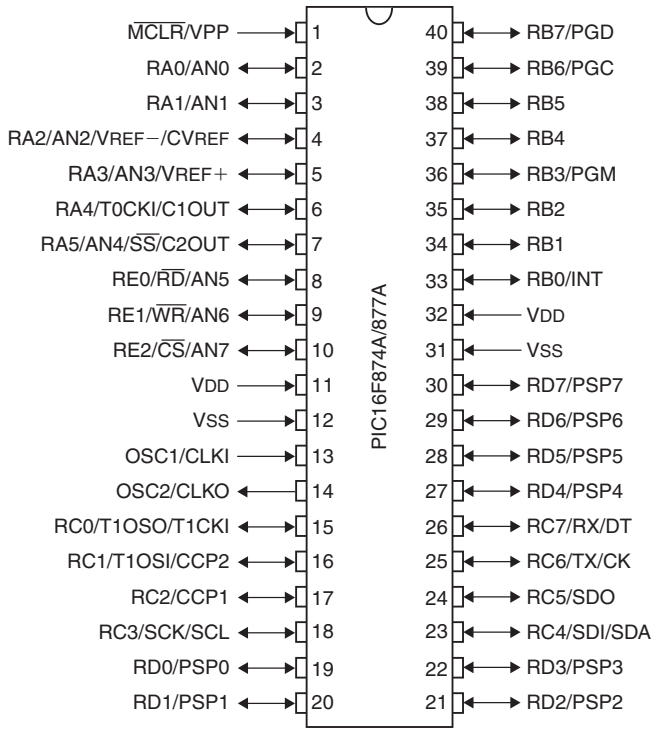
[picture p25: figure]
MCLR/VPP; RA2/AN2/VREF/CVREF; RA3/AN3/VREF-; RA4/T0CKI/C1OUT; RA5/AN4/SS/C2OUT; VDD; VSS; OSC1/CLKI; OSC2/CLKO; RC0/T1OSO/T1CKI; RC1/T1OSI/CCP2; RC3/SCK/SCL; RD0/PSP0; RD1/PSP1; RC2/CCP1; RB7/PGD; RB6/PGC; RB3/PGM; RB0/INT; RD7/PSP7; RD6/PSP6; RD5/PSP5; RD4/PSP4; RC5/SDO; RC4/SDI/SDA; RD3/PSP3; RD2/PSP2; PIC16F874A/877A

368 bytes of RAM, 256 bytes of nonvolatile EEPROM memory, 33 I/O pins, 8 multiplexed A/D converters with 10 bits of resolution, PWM generator, three timers, an analog capture and comparator circuit, USART, and internal and external interrupt facilities. Figure 1.4 shows the pin confi guration of this microcontroller.

Table 1.3: PIC16F84 Microcontroller Pin Descriptions

Pin | Description | Pin | Description
1 | RA2—PORTA bit 2 | 10 | RB4—PORTB bit 4
2 | RA3—PORTA bit 3 | 11 | RB5—PORTB bit 5
3 | RA4/T0CK1—PORTA bit 4/Counter clk | 12 | RB6—PORTB bit 6
4 | MCLR—Master clear | 13 | RB7—PORTB bit 7
5 | Vss—Gnd | 14 | Vdd—-V supply
6 | RB0/INT—PORTB bit 0 | 15 | OSC2
7 | RB1—PORTB bit 1 | 16 | OSC1
8 | RB2—PORTB bit 2 | 17 | RA0—PORTA bit 0
9 | RB3—PORTB bit 3 | 18 | RA1—PORTA bit 1
The PIC Microcontroller Family | 9

Figure 1.4: PIC16F877 Microcontroller Pin Confi guration

### 10 Chapter 1

PIC16F627: This is an 18-pin microcontroller with 1024 14 fl ash program memory. The device offers 224 bytes of RAM, 128 bytes of nonvolatile EEPROM memory, 16 I/O pins, two 8-bit timers, one 16-bit timer, a watchdog, and comparator circuits. This microcontroller is similar to PIC16F84, but offers more I/O pins, more program memory, and a lot more RAM. In addition, PIC16F627 is more suited to applications that require more than one timer. Figure 1.5 shows the pin confi guration of this microcontroller.

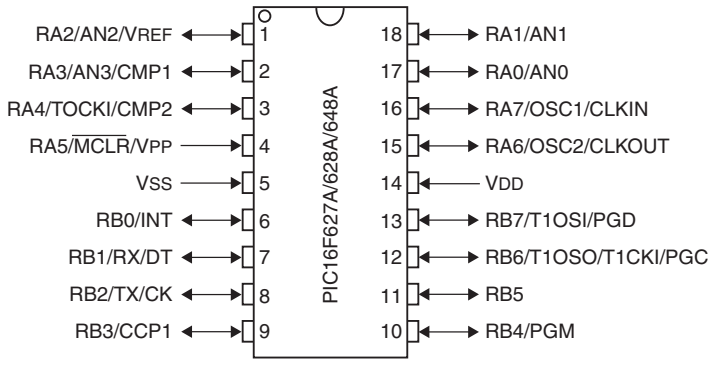
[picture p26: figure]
RA2/AN2/VREF; RA3/AN3/CMP1; RA4/TOCKI/CMP2; RA5/MCLR/VPP; VSS; RB0/INT; RB3/CCP1; RA7/OSC1/CLKIN; RA6/OSC2/CLKOUT; VDD; RB7/T1OSI/PGD; RB6/T1OSO/T1CKI/PGC; RB4/PGM; 10 PIC¹⁶F627A/628A/648A

Figure 1.5: PIC16F627 Microcontroller Pin Confi guration

PIC16F676: Figure 1.6 shows a 14-pin microcontroller that is becoming very popular. The device offers 1024 14 fl ash program memory, 64 bytes of RAM, 12 I/O pins, 128 bytes of EEPROM, 8 multiplexed A/D converters, each with 10-bit resolution, one 8-bit timer, one 16-bit timer, and a watchdog. One of the advantages of this microcontroller is the built-in A/D converter.

1

2

3

4

VDD | 14

RA5/T1CKI/OSC1/CLKIN

RA4/T1G/OSC2/AN3/CLKOUT

RA3/MCLR/VPP

RC5

RC4

RC3/AN7

VSS

RA0/AN0/CIN-/ICSPDAT

RA1/AN1/CIN/VREF/ICSPCLK

RA2/AN2/COUT/T0CK/INT

RC0/AN4

RC1/AN5

RC2/AN6

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
PIC16F676

Figure 1.6: PIC16F676 Microcontroller Pin Confi gurationm

PIC16F73: This is a powerful 28-pin microcontroller with 4096 14 fl ash program memory, 192 bytes of RAM, 22 I/O pins, fi ve multiplexed 8-bit A/D converters, two 8-bit timers, one 16-bit timer, watchdog, USART, and I²
C bus compatibility. This device combines A/D

The PIC Microcontroller Family 11

converter, digital I/O, and serial I/O capability in a 28-pin medium size package. Figure 1.7 shows the pin confi guration of this microcontroller.

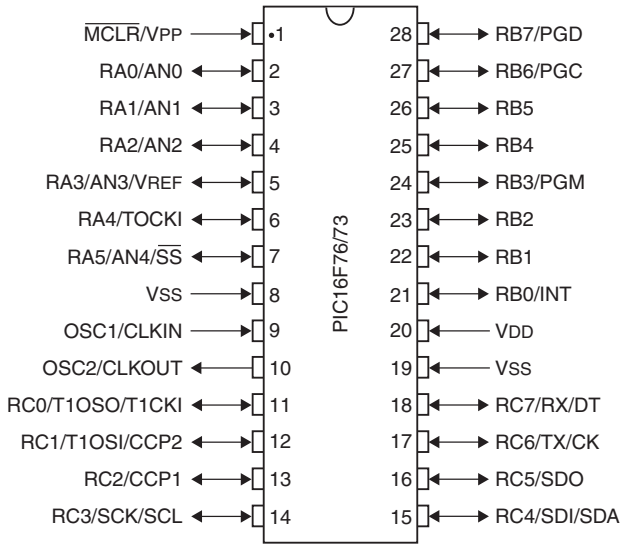
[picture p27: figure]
MCLR/VPP; RA3/AN3/VREF; RA4/TOCKI; VSS; OSC1/CLKIN; OSC2/CLKOUT; RC0/T1OSO/T1CKI; RC1/T1OSI/CCP2; RC2/CCP1; RC3/SCK/SCL; RB7/PGD; RB6/PGC; RB3/PGM; RB0/INT; VDD; RC5/SDO; RC4/SDI/SDA; PIC16F76/73

Figure 1.7: PIC16F73 Microcontroller Pin Confi guration

## 1.3 16-bit Instruction Word

The 16-bit microcontrollers are at the high end of the PIC microcontroller family. Most of the devices in this group can operate at up to 40 MHz, have 33 I/O pins, and three timers. They have 23 instructions in addition to the 35 instructions found on the 14-bit microcontrollers. Table 1.4 lists some of the devices in this family.

All memory for the PIC microcontroller family is internal and it is usually not very easy to extend this memory externally. No special hardware or software features are provided for

Table 1.4: Some 16-bit PIC Microcontrollers

Microcontroller | Program Memory | Data RAM | Max Speed (MHz) | I/O Ports | A/D Converter
17C43 | 4096 16 | 454 | 33 | 33 | –
17C752 | 8192 16 | 678 | 33 | 50 | 12
18C242 | 8192 16 | 512 | 40 | 23 | 5
18C252 | 16384 16 | 1536 | 40 | 23 | 5
18F4520 | 32768 16 | 1536 | 40 | 36 | 13

### 12 Chapter 1

extending either the program memory or the data memory. The program memory is usually suffi cient for small to medium size projects. But the data memory is generally small and may not be enough for medium to large projects unless a bigger and more expensive member of the family is chosen. For some large projects even this may not be enough and the designer may have to sacrifi ce the I/O ports to interface an external data memory, or to choose a microcontroller from a different manufacturer.

## 1.4 Inside a PIC Microcontroller

Although there are many models of microcontrollers in the PIC family, they all share some common features, such as program memory, data memory, I/O ports, and timers. Some devices have additional features such as A/D converters, USARTs and so on. Because of these common features, we can look at these attributes and cover the operation of most devices in the family.

### 1.4.1 Program Memory (Flash)

The program memory is where your program resides. In early microprocessors and microcontrollers the program memory was EPROM, which meant that it had to be erased using UV light before it could be reprogrammed. Most PIC microcontrollers nowadays are based on
fl ash technology, where the memory chip can be erased or reprogrammed using a programmer device. Most PIC microcontrollers can also be programmed without removing them from their circuits. This process (called in-circuit serial programming, or ISP) speeds up the development cycle and lowers the development costs. Although the program memory is mainly used
to store a program, there is no reason why it cannot be used to store constant data used in programs.

PIC microcontrollers can have program memories from 0.5 to over 16 K. A PicBasic program can have several pages of code and still fi t inside 1 K of program memory. The width of a 14-bit program memory is actually 14 bits. It is interesting to note that PICs are known as 8-bit microcontrollers. This is actually true as far as the width of the data memory is concerned, which is 8 bits wide. Microchip calls the 14 bits a word, even though a word is actually 16 bits wide.

When power is applied to the microcontroller or when the MCLR input is lowered to logic 0, execution starts from the Reset Vector, which is the fi rst word of the program memory.
Thus, the fi rst instruction executed after a reset is the one located at address 0 of the program memory. When the program is written in assembler language, the programmer has to use special instructions (called ORG) so that the fi rst executable instruction is loaded into address 0 of the program memory. High-level languages such as PicBasic or PicBasic Pro compile your program such that the fi rst executable statement in your program is loaded into the fi rst location of the program memory.

The PIC Microcontroller Family 13

### 1.4.2 Data Memory (RAM)

The data memory is used to store all of your program variables. This is a RAM, which means that all the data is lost when power is removed. The data memory is 8 bits wide and this is why the PIC microcontrollers are called 8-bit microcontrollers.

The data memory in a PIC microcontroller consists of banks, with some models having only two banks, some models four banks, and so on. A required bank of the data memory can be selected under program control.

### 1.4.3 Register File Map and Special Function Registers

Register File Map (RFM) is a layout of all the registers available in a microcontroller and this is extremely useful when programming the device, especially when using assembler language. The RFM is divided into two parts: the Special Function Registers (SFR), and the General Purpose Registers (GPR). For example, on a PIC16F84 microcontroller there are 68 GPR registers and these are used to store temporary data.

SFR is a collection of registers used by the microcontroller to control the internal operations of the device. Depending upon the complexity of the devices, the number of registers in the SFR varies. It is important that the programmer understands the functions of the SFR registers fully since they are used both in assembly language and in high-level languages.

Depending on the model of PIC microcontroller used, there could be other registers. For example, writing and reading from the EEPROM are controlled by SFR registers EECON1, EECON2, EEADR, and EEDATA. Fortunately, PicBasic and PicBasic Pro compilers provide simple high-level instructions for writing to and reading from the EEPROM and thus you do not need to know how to load these registers if you are programming in these languages.

Some of the important SFR registers that you may need to confi gure while programming using a high-level language are

- OPTION register
- I/O registers
- Timer registers
- INTCON register
- A/D converter registers

The functions and the bit defi nitions of these registers are described in detail in the following sections.

### 1.4.3.1 OPTION Register

This register is used to set up various internal features of the microcontroller and is named as OPTION_REG. This is a readable and writable register containing various control bits

### 14 Chapter 1

Bit 7: PORTB Pull-up Enable
1: PORTB pull-ups disabled 0: PORTB pull-ups enabled

Bit 6: INT Interrupt Edge Detect
1: Interrupt on rising edge of INT input 0: Interrupt on falling edge of INT input

Bit 5: TMR0 Clock Source
1: T0CK1 pulse
0: Internal oscillator

Bit 4: TMR0 Source Edge Select
1: Increment on HIGH to LOW of T0CK1 0: Increment on LOW to HIGH of T0CK1

Bit 3: Prescaler Assignment
1: Prescaler assigned to Watchdog Timer 0: Prescaler assigned to TMR0

Bit 2-0: Prescaler Rate
000 | 1:2
001 | 1:4
010 | 1:8
011 | 1:16
100 | 1:32
101 | 1:64
110 | 1:128
111 | 1:256
7 | | 5 6 | 4 | 3 | 2 | 1 | 0
RBPU | INTEDG | T0CS | T0SE | PSA | PS2 | PS1 | PS0

Figure 1.8: OPTION_REG Bit Defi nitions

to confi gure the on-chip timer and the watchdog timer. This register is at address 81 (hexadecimal) of the microcontroller and its bit defi nitions are given in Figure 1.8. The OPTION REG register is also used to control the external interrupt pin RB0. This pin can be set up to generate an interrupt—for example, when it changes from logic 0 to logic 1. The microcontroller then suspends the main program execution and jumps to the interrupt service routine (ISR) to service the interrupt. Upon return from the interrupt, normal processing resumes.

For example, to confi gure the INT pin so that external interrupts are accepted on the rising edge of the INT pin, the following bit pattern should be loaded into the OPTION_REG:

X1XXXXXX

where X is a don’t care bit and can be a 0 or a 1. We shall see later how to confi gure various bits of this register.

The PIC Microcontroller Family 15

### 1.4.3.2 I/O Registers

These registers are used for the I/O control. Every I/O port in the PIC microcontroller has two registers: port data register and port direction control register.

Port data register has the same name as the port it controls. For example, the PIC16F84 microcontroller has two port data registers, PORTA and PORTB. A PIC16F877 microcontroller has fi ve port data registers, PORTA, PORTB, PORTC, PORTD, and PORTE. Eight bits of data can be sent to any port, or 8 bits of data can be read from the ports. It is also possible to read or write to individual port pins. For example, any bit of a given port can be set or cleared, or data can be read from one or more port pins at the same time.

Ports in a PIC microcontroller are bidirectional. Thus, each pin of a port can be used as an input or an output pin. Port direction control register confi gures the port pins as either inputs or outputs. This register is called the TRIS register and every port has a TRIS register named after its port name. For example, TRISA is the direction control register for PORTA. Similarly, TRISB is the direction control register for PORTB and so on.

Setting a bit in the TRIS register makes the corresponding port register pin an input. Clearing a bit in the TRIS register makes the corresponding port pin an output. For example, to make bits 0 and 1 of PORTB input and the other bits output, we have to load the TRISB register with the bit pattern.

00000011

Figure 1.9 shows the TRISB register and the direction of PORTB pins.

TRISB

PORTB

0 | 0 | 0 | 0 | 0 | 0 | 1 1
7 | 6 | 5 | 4 | 3 | 2 | 1 | 0

Figure 1.9: TRISB and PORTB Direction

Note that port data register and port direction control registers can be accessed directly using the PicBasic Pro compiler. For example, as we shall see later, TRISB register can be set to 3 and data can be read from PORTB into a variable named CNT by the PicBasic Pro instructions:

TRISB 3
CNT PORTB

### 16 Chapter 1

The PicBasic compiler has no direct register control instructions and, as we shall see later, we have to use the PEEK and POKE instructions. PEEK is used to read data from a register and POKE is used to send data to a register.

When we use the PEEK and POKE instructions, we have to specify the register address of the register we wish to access. The register addresses of port registers are (the “$” character specifi es that the number is in hexadecimal format):

Thus, for the above example, the required PicBasic instructions will be

POKE $86, 3
PEEK $06, CNT

### 1.4.3.3 Timer Registers

Depending on the model used, some PIC microcontrollers have only one timer, and some may have up to three timers. In this section we shall look at the PIC16F84 microcontroller, which has only one timer. The extension to several timers is similar and we shall see in the projects section how to use more than one timer.

The timer in the PIC16F84 microcontroller is an 8-bit register (called TMR0), which can
be used as a timer or a counter. When used as a counter, the register increments each time a clock pulse is applied to pin T0CK1 of the microcontroller. When used as a timer, the register increments at a rate determined by the system clock frequency and a prescaler selected by register OPTION_REG. Prescaler rates vary from 1:2 to 1:256. For example, when using a 4-MHz clock, the basic instruction cycle is 1 s (the clock is internally divided by four). If we select a prescaler rate of 1:16, the counter will be incremented at every 16 s.

The TMR0 register has address 01 in the RAM.

Ports | Address (Hexadecimal)
PORTA | $05
PORTB | $06
PORTC | $07
PORTD | $08
PORTE | $09
TRISA | $85
TRISB | $86
TRISC | $87
TRISD | $88
TRISE | $89

The PIC Microcontroller Family 17

A timer interrupt is generated when the timer overfl ows from 255 to 0. This interrupt can be enabled or disabled by our program. Thus, for example, if we need to generate interrupts at intervals of 200 s using a 4-MHz clock, we can select a prescaler value of 1:4 and enable timer interrupts. The timer clock rate is then 4 s. For a time-out of 200 s, we have to send 50 clocks to the timer. Thus, the TMR0 register should be loaded with 256 – 50 206—i.e., a count of 50 before an overfl ow occurs.

The watchdog timer’s oscillator is independent from the CPU clock and the time-out is 18 ms. To prevent a time-out condition the watchdog must be reset periodically via software. If the watchdog timer is not reset before it times out, the microprocessor will be forced to jump to the reset address. The prescaler can be used to extend the time-out period and valid rates are 1, 2, 4, 8, 16, 32, 64, and 128. For example, when set to 128, the time-out period is about 2 s (18 128 2304 ms). The watchdog timer can be disabled during programming of the device if it is not used.

Since the timer is a very important part of the PIC microcontrollers, more detailed information is given on its operation below.

### 1.4.3.4 TMR0 and Watchdog

TMR0 and a watchdog are found in nearly all PIC microcontrollers. Figure 1.10 shows the functional diagram of TMR0 and the watchdog circuit. The operation of the watchdog circuit is as described earlier and only the TMR0 circuit is described in this section.

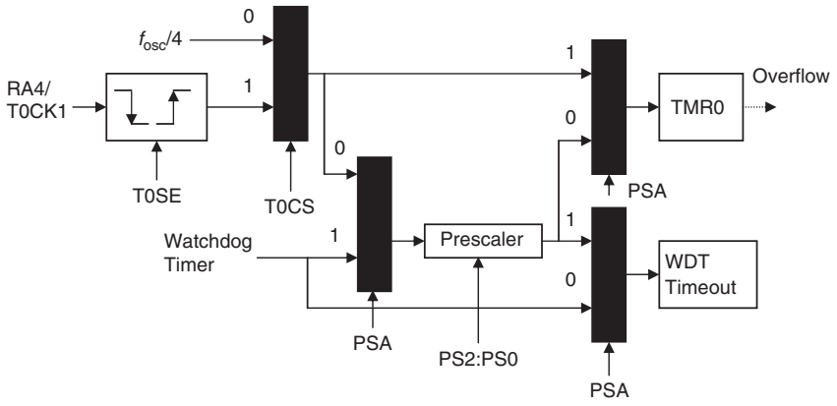
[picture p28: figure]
fosc/4; PSA; Watchdog Timer; Prescaler; TMR0; WDT Timeout; Overflow

The source of input for TMR0 is selected by bit T0CS of OPTION_REG and it can be either from the microcontroller oscillator fosc divided by 4, or it can be an external clock applied to the RA4/T0CK1 input. Here, we will only look at using the internal oscillator. If a 4-MHz crystal is used, the internal oscillator frequency is fosc/4 1 MHz, which corresponds to

Figure 1.10: TMR0 and Watchdog Circuit

### 18 Chapter 1

a period of T 1/f 106
, or 1 s. TMR0 is then selected as the source for the prescaler by clearing the PSA bit of OPTION_REG. The required prescaler value is selected by bits PS0 to PS2 as shown in Fig. 1.8. Bit PSA should then be cleared to 0 to select the prescaler for the timer. All the bits are confi gured now and the TMR0 register increments each time a pulse is applied by the internal oscillator. TMR0 register is 8 bits wide and it counts up to 255, then creates an overfl ow condition, and continues counting from 0. When TMR0 changes from 255 to 0 it generates a timer interrupt if timer interrupts and global interrupts are enabled (see INTCON register; an interrupt will be generated if GIE and TMR0 bits of INTCON are both set to 1). See Section 1.4.6 on Interrupts for more information.

By loading a value into the TMR0 register we can control the count until an overfl ow occurs. The formula given below can be used to calculate the time it will take for the timer to overfl ow (or to generate an interrupt) given the oscillator period, value loaded into the timer and the prescaler value.

Overfl ow time 4 TOSC Prescaler (256 – TMR0) | (1.1)

where
Overfl ow time is in s
TOSC is the oscillator period in s
Prescaler is the prescaler value chosen using OPTION_REG
TMR0 is the value loaded into TMR0 register

For example, assume that we are using a 4-MHz crystal, and the prescaler is chosen as 1:8 by setting bits PS2:PS0 to “010”. Also assume that the value loaded into the timer register TMR0 is decimal 100. The overfl ow time is then given by

4 MHz clock has a period, T 1/f 0.25 s

Using the above formula,

Overfl ow time 4 0.25 8 (256 – 100) 1248 s. Thus, the timer will overfl ow after 1.248 µs and a timer interrupt will be generated if the timer interrupt and global interrupts are enabled.

What we normally need is to know what value to load into the TMR0 register for a required Overfl ow time. This can be calculated by modifying Eq. (1.1) as

TMR0 256 – (Overfl ow time)/(4 TOSC Prescaler) | (1.2)

For example, suppose that we want an interrupt to be generated after 500 s and the clock and the prescaler values are as before. The value to be loaded into the TMR0 register can be calculated using Eq. (1.2) as

TMR0 256 – 500/(4 0.25 8) 193.5

The nearest number we can load into the TMR0 register is 193.

The PIC Microcontroller Family 19

Table 1.5 gives the values that should be loaded into the TMR0 register for different Overfl ow times. In this table a 4-MHz crystal is assumed and the table gives the result as the prescaler value is changed from 2 to 256.

Table 1.5: Required TMR0 Values for Different Overfl ow Times

Time to | Prescaler
2 | 4 | 8 | 16 | 32 | 64 | 128 | 256
100 | 206 | 231 | 243 | 250 | 253 | 254 | – | –
200 | 156 | 206 | 231 | 243 | 250 | 253 | 254 | –
300 | 106 | 181 | 218 | 237 | 246 | 251 | 253 | 255
400 | 56 | 156 | 206 | 231 | 243 | 250 | 253 | 254
500 | 6 | 131 | 193 | 224 | 240 | 248 | 252 | 254
600 | – | 106 | 181 | 218 | 237 | 16 | 251 | 253
700 | – | 81 | 168 | 212 | 234 | 245 | 250 | 253
800 | – | 56 | 156 | 206 | 231 | 243 | 250 | 253
1,000 | – | 6 | 131 | 193 | 225 | 240 | 248 | 252
5,000 | – | – | – | – | 100 | 178 | 77 | 236
10,000 | – | – | – | – | – | 100 | 178 | 217
20,000 | – | – | – | – | – | – | 100 | 178
30,000 | – | – | – | – | – | – | – | 139
40,000 | – | – | – | – | – | – | – | 100
50,000 | – | – | – | – | – | – | – | 60
60,000 | – | – | – | – | – | – | – | 21

Overfl ow (s)

### 1.4.3.5 TMR1

Although TMR0 is the basic timer found in nearly all PIC microcontrollers, some devices have several timers, such as TMR0, TMR1, and TMR2. Additional timers give added functionality to a microcontroller. In this section the operation of TMR1 will be described in detail.

TMR1 is a 16-bit timer, consisting of two 8-bit registers TMR1H and TMR1L. As shown
in Fig. 1.11, a prescaler is used with TMR1 and the available prescaler values are only 1, 2, 4, and 8.

Register T1CON controls the operation of TMR1. The bit defi nition of this register is shown in Fig. 1.12. TMR1 can operate either as a timer or as a counter, selected by bit TMR1CS of T1CON. When operated in timer mode, TMR1 increments every oscillator frequency fosc/4.

### 20 Chapter 1

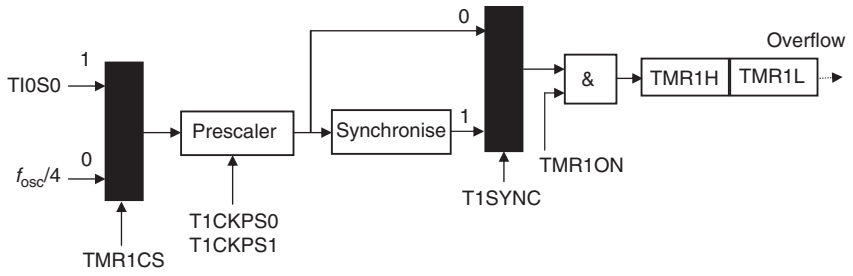
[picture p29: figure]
TMR1CS; Prescaler; T1CKPS0 T1CKPS1; Synchronise; T1SYNC; TMR1ON; TMR1H TMR1L; fosc/4; Overflow

TMR1 can be enabled or disabled by setting or clearing control bit TMR1ON. TMR1 can count from 0 to 65,535 and it generates an overfl ow when changing from 65,535 to 0. A timer interrupt is generated if the TMR1 interrupt enable bit TMR1IE is enabled and also the global interrupts are enabled by register INTCON.

Figure 1.11: TMR1 Structure

Figure 1.12: T1CON Bit Defi nitions

Bit 7: Unused

Bit 6: Unused

Bit 5–4: Timer1 Input Clock Prescale Select Bits
11 | 1:8 prescale value
10 | 1:4 prescale value
01 | 1:2 prescale value
00 | 1:1 prescale value

Bit 3: Timer1 Oscillator Enable Bit
1: Oscillator is enabled
0: Oscillator is disabled

Bit 2: Timer1 External Clock Input Synchronization Select Bit When TMR1CS 1:
1: Do not synchronize external clock input
0: Synchronize external clock input
When TMR1CS 0:
This bit is ignored. Timer1 uses internal clock

Bit 1: Timer1 Clock Source Select Bit
1: External clock from pin TIOSO (on rising edge) 0: Internal clock (ƒosc /4)

Bit 0: Timer1 On Bit
1: Enable Timer1
0: Stops Timer1
7 | | 5 6 | 4 | 3 | 2 | 1 | 0
| | TICKPS1 | TICKPS0 | TIOSCEN | TISYNC | TMR1CS | TMR1ON

The PIC Microcontroller Family 21

When TMR1 is operated in counter mode, it increments on every rising edge (from logic 0 to logic 1) of the clock input.

### 1.4.3.6 TMR2

TMR2 is an 8-bit timer with a prescaler and a postscaler and it has an 8-bit period register PR2. This timer is controlled by register T2CON whose bit defi nitions are given in Fig. 1.13. The prescaler options are 1, 4, and 16 only and are selected by T2CKPS1 and T2CKPS0 bits of T2CON. TMR2 increments from 0, until it matches PR2, and then resets to 0 on the next cycle. Then the cycle is repeated. TMR2 can be shut off by clearing TMR2ON of T2CON register to minimize power consumption.

### 1.4.3.7 INTCON Register

This is the interrupt control register. This register is at address 0 and 8B (hexadecimal) of the microcontroller RAM and the bit defi nitions are given in Fig. 1.14. For example, to enable interrupts so that external interrupts from pin INT (RB0) can be accepted on a PIC16F84, the following bit pattern should be loaded into register INTCON:

1XX1XXXX

Similarly, to enable timer interrupts, bit 5 of INTCON must be set to 1.

Figure 1.13: T2CON Bit Defi nitions

Bit 7: Unused

Bit 6-3: Timer2 Output Postscale Select Bits
0000 | 1:1 Postscale
0001 | 1:2 Postscale
0010 | 1:3 Postscale
1111 1:16 Postscale

Bit 2: Timer2 On Bit
1: Timer2 is On
0: Timer2 is Off

Bit 1-0: Timer2 Clock Prescale Select Bits
00 | Prescaler is 1
01 | Prescaler is 4
10 | Prescaler is 16
11 | Prescaler is 16
7 | | 5 6 | 4 | 3 | 2 | 1 | 0
| TOUTPS3 | TOUTPS2 | TOUTPS1 | TOUTPS0 | TMR2ON | T2CKPS1 | T2CKPS0

### 22 Chapter 1

### 1.4.3.8 A/D Converter Registers

The A/D converter is used to interface analog signals to the microcontroller. The A/D converts analog signals (e.g., voltage) into digital form so that they can be connected to a computer. A/D converter registers are used to control the A/D converter ports. On most PIC microcontrollers equipped with A/D, PORTA pins are used for analog input and these port pins are shared between digital and analog functions.

PIC16F876 includes fi ve A/D converters. Similarly, PIC16F877 includes eight A/D converters. There is actually only one A/D converter, as shown in Fig. 1.15, and the inputs are multiplexed and they share the same converter. The width of the A/D converter can be
8 bits or 10 bits. Both PIC16F876 and PIC16F877 have 10-bit converters. PIC16F73 has 8-bit converters. An A/D converter requires a reference voltage to operate. This reference voltage is

Bit 7: Global Interrupt Enable
1: Enable all un-masked interrupts 0: Disable all interrupts

Bit 6: EE Write Complete Interrupt
1: Enable EE write complete interrupt 0: Disable EE write complete interrupt

Bit 5: TMR0 Overflow Interrupt
1: Enable TMR0 interrupt
0: Disable TMR0 interrupt

Bit 4: INT External Interrupt
1: Enable INT External Interrupt 0: Disable INT External Interrupt

Bit 3: RB Port Change Interrupt
1: Enable RB port change interrupt 0: Disable RB port change interrupt

Bit 2: TMR0 Overflow Interrupt Flag
1: TMR0 has overflowed
0: TMR0 did not overflow

Bit 1: INT Interrupt Flag
1: INT interrupt occurred
0: INT interrupt did not occur

Bit 0: RB Port Change Interrupt Flag
1: One or more of RB4-RB7 pins changed state 0: None of RB4-RB7 changed state
7 | | 5 6 | 4 | 3 | 2 | 1 | 0
GIE | EEIE | T0IE | INTE | RBIE | T0IF | INTF | RBIF

Figure 1.14: INTCON Register Bit Defi nitions

The PIC Microcontroller Family 23

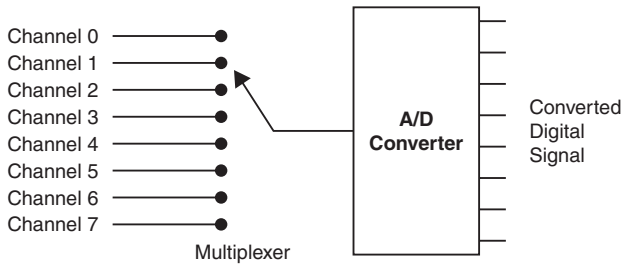
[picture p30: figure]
A/D Converter; Channel 0 Channel 1 Channel 2 Channel 3 Channel 4 Channel 5 Channel 6 Channel 7; Converted Digital Signal; Multiplexer

chosen by programming the A/D converter registers and is typically 5 V. Thus, if we are using a 10-bit converter (1024 quantization levels), the resolution of our converter will be 5/1024 0.00488 V, or 4.88 mV; i.e., we can measure analog voltages with a resolution of 4.88 mV. For example, if the measured analog input voltage is 4.88 mV we get the 10-bit digital number “0000000001”; if the analog input voltage is 2 4.88 9.76 mV, the 10-bit converted number will be “0000000010”; if the analog input voltage is 3 4.88 14.64 mV, the converted number will be “0000000011”; and so on.

In a similar way, if the reference voltage is 5 V and we are using an 8-bit converter (256 quantization levels), the resolution of the converter will be 5/256 19.53 mV. For example, if the measured input voltage is 19.53 mV we get the 8-bit number “00000001”; if the analog input voltage is 2 19.53 39.06 mV we get the 8-bit number “00000010”; and so on.

The A/D converter is controlled by registers ADCON0 and ADCON1. The bit pattern of ADCON0 is shown in Fig. 1.16. ADCON0 is split into four parts; the fi rst part consists of the highest two bits ADCS1 and ADCS0 and they are used to select the conversion clock. The internal RC oscillator or the external clock can be selected as the conversion clock as in the following table:

00 | External clock/2
01 | External clock/8
10 | External clock/32
11 | Internal RC clock

The second part of ADCON0 consists of the three bits CHS2, CHS1, and CHS0. These are the channel select bits, and they select which input pin is routed to the A/D converter. The selection is as follows:

CHS2:CHS1:CHS0
000 | Channel 0
001 | Channel 1
010 | Channel 2

Figure 1.15: Multiplexed A/D Structure

### 24 Chapter 1

011 | Channel 3
100 | Channel 4
101 | Channel 5
110 | Channel 6
111 | Channel 7

The third part of ADCON0 is the single GO/DONE bit. This bit has two functions: fi rst, by setting the bit it starts the A/D conversion. Second, the bit is cleared when the conversion is complete and this bit can be checked to see whether or not the conversion is complete.

The fourth part of ADCON0 is also a single bit, ADON, which is set to turn on the A/D converter circuitry.

ADRESH and ADRESL are the A/D converter result registers. ADRESL is the low byte and ADRESH is the upper 2 bits (if a 10-bit converter is used). We shall see how to confi gure the result of the conversion later.

ADCON1 is the second A/D control register. This register controls the format of converted data and mode of the PORTA inputs. The bit format of this register is shown in Fig. 1.17.

Figure 1.16: ADCON0 Bit Defi nitions

Bit 7-6: A/D Converter Clock Select
00 | ƒosc/2
01 | ƒosc/8
10 | ƒosc/32
11 | Internal RC oscillator

Bit 5-3: A/D Channel Select
000 | Channel 0
001 | Channel 1
010 | Channel 2
011 | Channel 3
100 | Channel 4
101 | Channel 5
110 | Channel 6
111 | Channel 7

Bit 2: GO/DONE Bit
1: Start conversion
0: A/D conversion is complete

Bit 1: Not used

Bit 0: ADON Bit
1: Turn ON A/D circuit
0: Turn OFF A/D circuit
7 | | 5 6 | 4 | 3 | 2 | 1 | 0
ADCS1 | ADCS0 | CHS2 | CHS1 | CHS0 | GO/DONE | – | ADON

The PIC Microcontroller Family 25

Bit 7 is called ADFM and when this bit is 0 the result of the A/D conversion is left justifi ed; when it is 1, the result of the A/D conversion is right justifi ed. If we have an 8-bit converter, we can clear ADFM and just read ADRESH to get the 8-bit converted data. If we have a 10-bit converter, we can set ADFM to 1 and the 8 bits of the result will be in ADRESL, and 2 bits of the result will be in the lower bit positions of ADRESH. The remaining 6 positions of ADRESH (bit 2 to bit 7) will be cleared to zero.

Bits PCFG0-3 control the mode of PORTA pins. As seen in Fig. 1.17, a PORTA pin can be programmed to be a digital pin or an analog pin. For example, if we set PCFG0-3 to “0110” then all PORTA pins will be digital I/O pins. PCFG0-3 bits can also be used to defi ne the reference voltage for the A/D converter. As we shall see in the projects section of the book, the reference voltage Vref is usually set to be equal to the supply voltage (Vdd), and Vref is set to be equal to Vss. This causes the A/D reference voltage to be -5 V.

### 1.4.4 Oscillator Circuits

An oscillator circuit is used to provide a microcontroller with a clock. A clock is needed so that the microcontroller can execute a program.

Bit 7: A/D Converter Result Format Select 1: A/D converter output is right justified 0: A/D converter output is left justified

Bit 6: Not used

Bit 5: Not used

Bit 4: Not used

Bit 3-0: Port Assignment and Reference Voltage Selection (see Figure 1.17)

7 | 6 | 5 | 4 | 3 | 2 | 1 | 0
ADFM | | | | PCFG3 | PCFG2 | PCFG1 | PCFG0

PIC microcontrollers have built-in oscillator circuits and this oscillator can be operated in one of fi ve modes.

- LP—Low-power crystal
- XT—Crystal/resonator
- HS—High-speed crystal/resonator
- RC resistor–capacitor
- No external components (only on some PIC microcontrollers).

### 26 Chapter 1

In LP, XT, or HS modes, an external oscillator can be connected to the OSC1 input as shown in Fig. 1.18. This can be a crystal-based oscillator, or simple logic gates can be used to design an oscillator circuit.

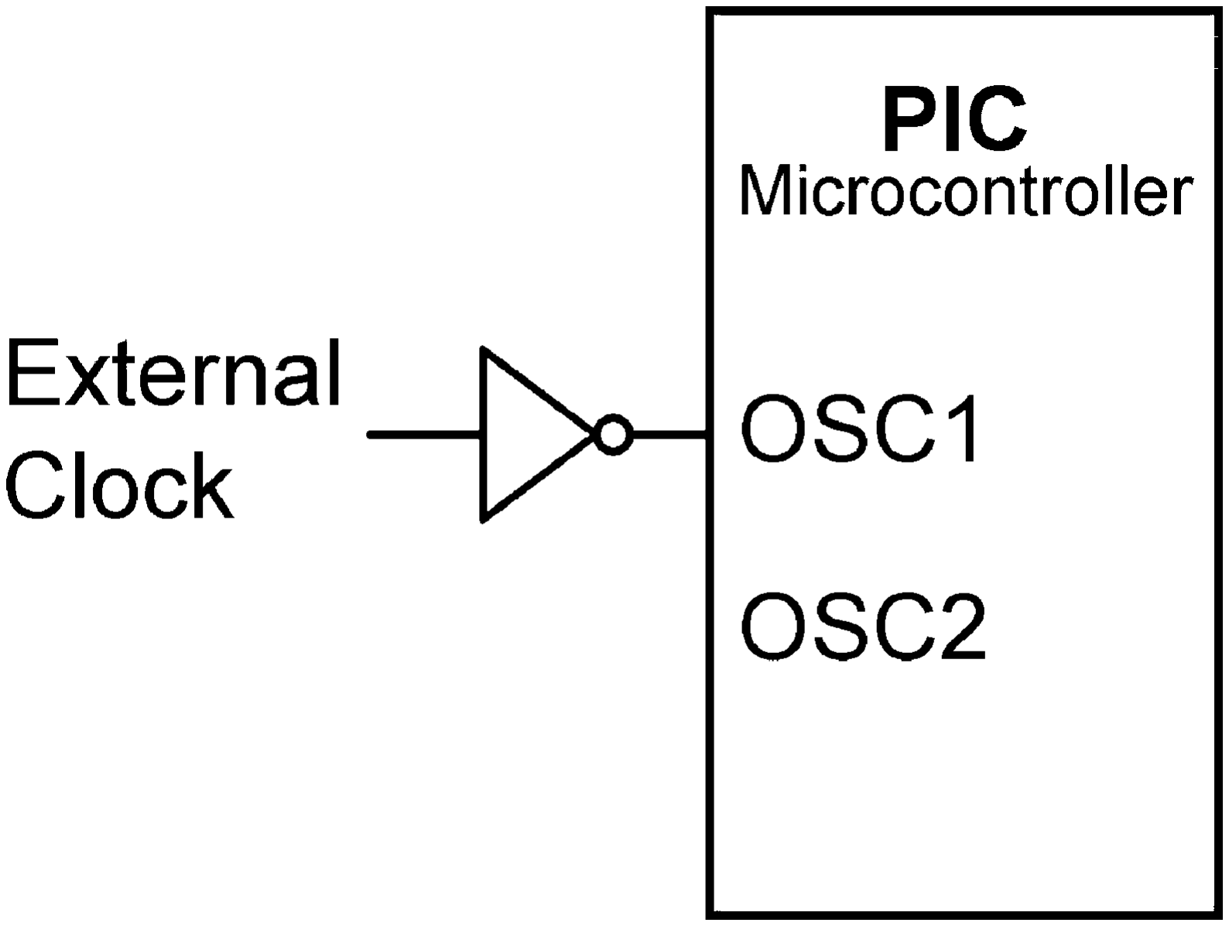
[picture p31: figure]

Figure 1.18: Using an External Oscillator

### 1.4.4.1 Crystal Operation

As shown in Fig. 1.19, in this mode of operation an external crystal and two capacitors are connected to the OSC1 and OSC2 inputs of the microcontroller. The capacitors should be chosen as in Table 1.6. For example, with a crystal frequency of 4 MHz, two 22-pF capacitors can be used.

Figure 1.17: ADCON1 Bit Defi nitions

PCFG3-PCFG0 | AN7 | AN6 | AN5 | AN4 | AN3 | AN2 | AN1 | AN0 | Vref- | Vref
0000 | A | A | A | A | A | A | A | A | Vdd | Vss
0001 | A | A | A | A | Vref- | A | A | A | RA3 | Vss
0010 | D | D | D | A | A | A | A | A | Vdd | Vss
0011 | D | D | D | A | Vref- | A | A | A | RA3 | Vss
0100 | D | D | D | D | A | D | A | A | Vdd | Vss
0101 | D | D | D | D | Vref- | D | A | A | RA3 | Vss
0110 | D | D | D | D | D | D | D | D | Vdd | Vss
0111 | D | D | D | D | D | D | D | D | Vdd | Vss
1000 | A | A | A | A | Vref- | Vref | A | A | RA3 | RA2
1001 | D | D | A | A | A | A | A | A | Vdd | Vss
1010 | D | D | A | A | Vref- | A | A | A | RA3 | Vss
1011 | D | D | A | A | Vref- | Vref | A | A | RA3 | RA2
1100 | D | D | D | A | Vref- | Vref | A | A | RA3 | RA2
1101 | D | D | D | D | Vref- | Vref | A | A | RA3 | RA2
1110 | D | D | D | D | D | D | D | A | Vdd | Vss
1111 | D | D | D | D | Vref- | Vref | D | A | RA3 | RA2

The PIC Microcontroller Family 27

### 1.4.4.2 Resonator Operation

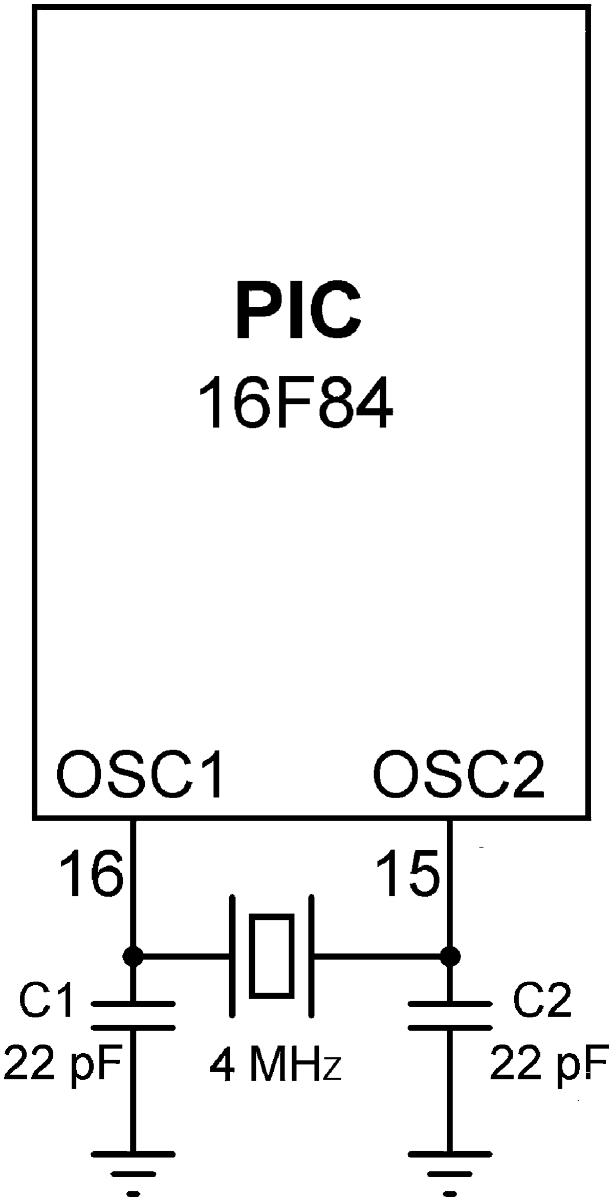
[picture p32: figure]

Resonators are available from 4 to about 8 MHz. They are not as accurate as crystal-based oscillators. Resonators are usually 3-pin devices and the two pins at either side are connected to OSC1 and OSC2 inputs of the microcontroller. The middle pin is connected to the ground. Figure 1.20 shows how a resonator can be used in a PIC microcontroller circuit.

### 1.4.4.3 RC Oscillator

For applications where the timing accuracy is not important, we can connect an external resistor and a capacitor to the OSC1 input of the microcontroller as in Fig. 1.21. The oscillator frequency depends upon the values of the resistor and capacitor (see Table 1.7), the supply voltage, and to the temperature. For most applications, using a 5 K resistor with a 20-pF capacitor gives about 4 MHz and this may be acceptable in non-time-critical applications.

Figure 1.19: Crystal Oscillator Circuit

Table 1.6: Capacitor Selection for Crystal Operation

Mode | Frequency | C1, C2
LP | 32 kHz | 68–100 pF
LP | 200 kHz | 15–33 pF
XT | 100 kHz | 100–150 pF
XT | 2 MHz | 15–33 pF
XT | 4 MHz | 15–33 pF
HS | 4 MHz | 15–33 pF
HS | 10 MHz | 15–33 pF

### 28 Chapter 1

### 1.4.4.4 Internal Oscillator

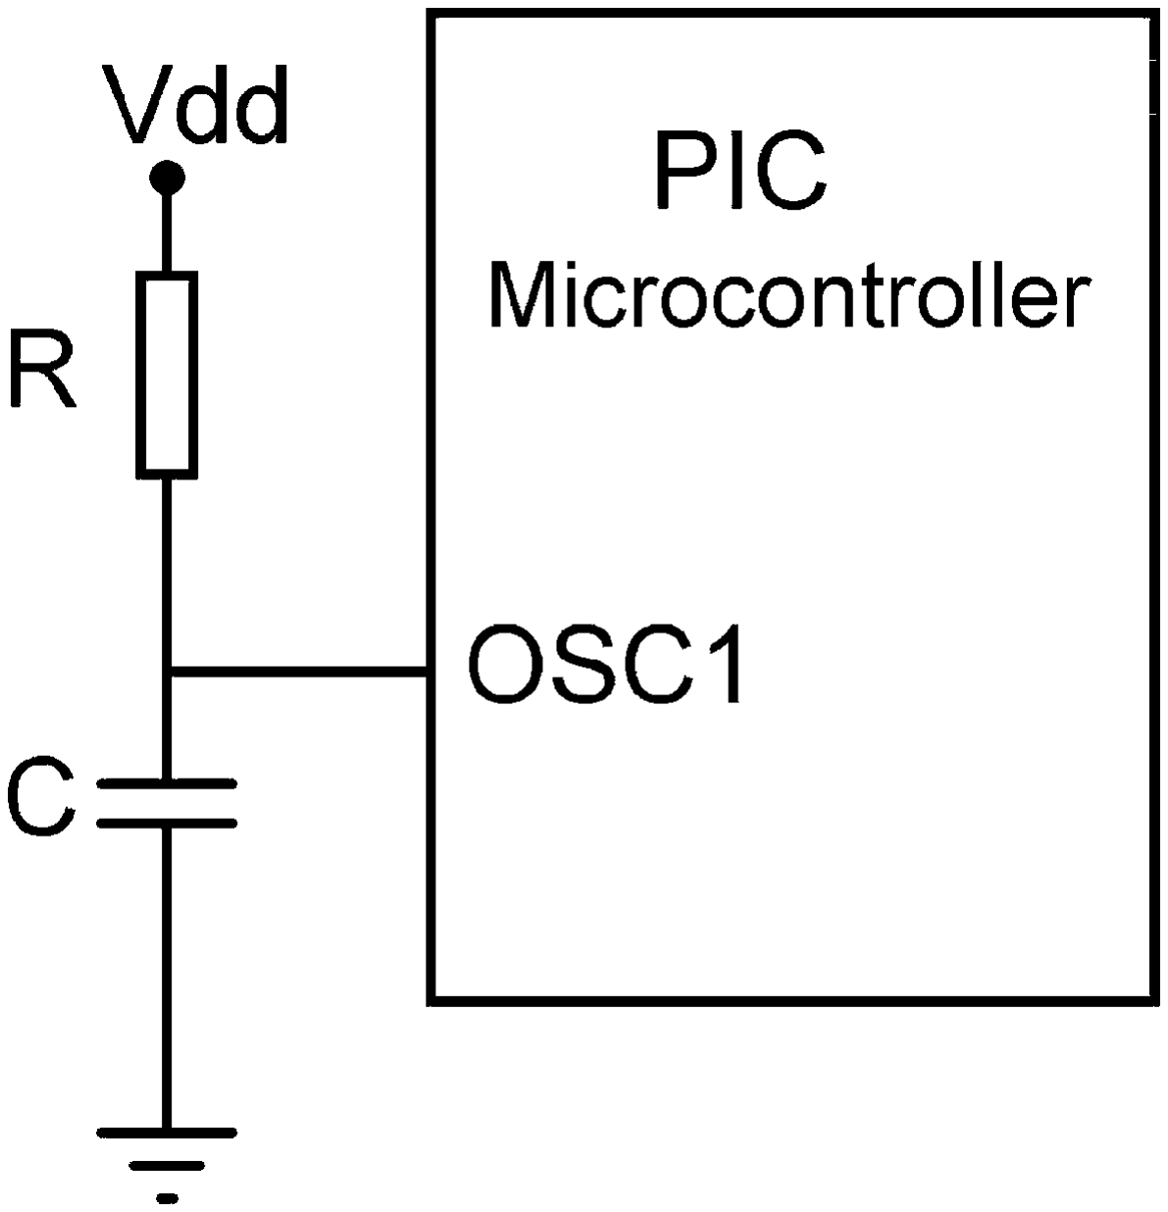
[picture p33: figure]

Some PIC microcontrollers (e.g., PIC12C672 and PIC16F628) have built-in oscillator circuits and they do not require any external timing components. The built-in oscillator is usually set

Figure 1.20: Resonator Oscillator Circuit

Figure 1.21: RC Oscillator Circuit

Table 1.7: RC Oscillator Component Selection

C | R | Frequency
20 pF | 5 K | 4.61 MHz
| 10 K | 2.66 MHz
| 100 K | 311 kHz
100 pF | 5 K | 1.34 MHz
| 10 K | 756 kHz
| 100 K | 82.8 kHz
300 pF | 5 K | 428 kHz
| 10 K | 243 kHz
| 100 K | 26.2 kHz

The PIC Microcontroller Family 29

to operate at 4 MHz and is selected during the programming of the device. For example, the PIC16F62X series of PIC microcontrollers can be operated with an internal resistor–capacitor-based 4-MHz oscillator (called mode INTRC). Additionally, a single resistor can be connected to pin RA7 of the microcontroller to create a variable oscillator frequency (called ER mode). For example, in the PIC16F62X microcontroller OSC1 and OSC2 pins are shared with the RA7 and RA6 pins, respectively. The internal oscillator frequency can be set by connecting
a resistor to pin RA7 as shown in Fig. 1.22. Depending on the value of this resistance, the oscillator frequency can be selected from 200 kHz to 10.4 MHz (see Table 1.8). When used in this mode, pin RA7 is not available as a digital I/O pin.

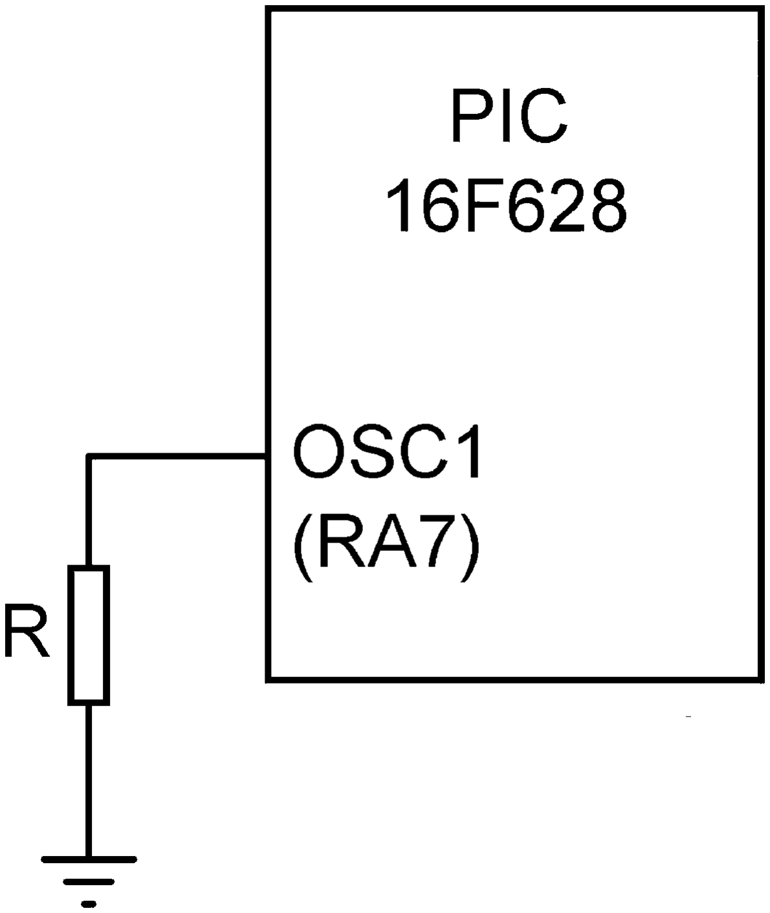
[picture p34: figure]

Figure 1.22: Changing the Internal Oscillator Frequency

The internal oscillator frequency of some microcontrollers (such as PIC16F630) can be calibrated so that more accurate timing pulses can be generated in time-critical applications (in serial communications, for example). In these microcontrollers an oscillator register called OSCCAL is used for the calibration of the oscillator frequency. A factory-calibrated oscillator constant is loaded into the last location of the memory. By copying this constant value into the oscillator register, we can have a more accurate 4-MHz clock frequency for our

Resistance | Frequency
0 | 10.4 MHz
1 K | 10.0 MHz
10 K | 7.4 MHz
20 K | 5.3 MHz
47 K | 3 MHz
100 K | 1.6 MHz
220 K | 800 kHz
470 K | 300 kHz
1 M | 200 kHz

Table 1.8: Resistor Value for the Internal Oscillator

### 30 Chapter 1

microcontroller. It is also possible to modify the OSCCAL register values in order to fi ne-tune the oscillator frequency.

As a practical example, the following PicBasic and PicBasic Pro statements can be used to copy the oscillator calibration constant from the last memory location into the OSCCAL register. These commands must be declared at the beginning of the programs.

DEFINE OSCCAL_1 K 1 | For 1 K core-size microcontrollers
DEFINE OSCCAL_2 K 1 | For 2 K core-size microcontrollers

Note that the oscillator constant can be erased during the erasing of the program memory. You should make a note of the value at the last location of the program memory before erasing the memory. If this value is known it can be loaded directly into the OSCCAL register at the beginning of our programs, as shown below (here it is assumed that the constant is $24).

OSCCAL $24

### 1.4.5 Reset Circuit

Reset is used to put the microcontroller into a known state. Normally when a PIC microcontroller is reset, execution starts from address 0 of the program memory. This is where the fi rst executable user program resides. The reset action also initializes various SFR registers inside the microcontroller.

PIC microcontrollers can be reset when one of the following conditions occur:

- Reset during power on (POR – Power On Reset)
- Reset by lowering MCLR input to logic 0
- Reset when the watchdog overfl ows.

As shown in Fig. 1.23, a PIC microcontroller is normally reset when power is applied to the chip and when the MCLR input is tied to the supply voltage through a 4.7 K resistor.

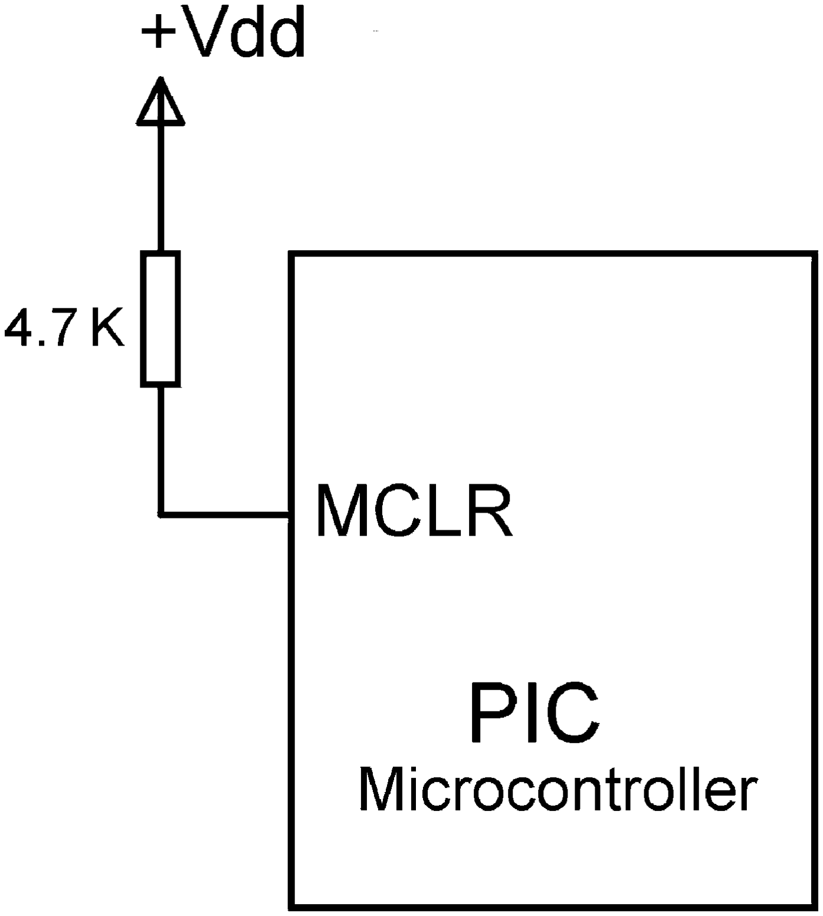
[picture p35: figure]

Figure 1.23: Using the Power on Reset

The PIC Microcontroller Family 31

There are many applications where we want to reset the microcontroller, for instance by pressing an external button. The simplest circuit to achieve an external reset is shown in Fig. 1.24. In this circuit, the MCLR input is normally at logic 1 and the microcontroller is operating normally. When the reset button is pressed, this pin goes to logic 0 and the microcontroller is reset. When the reset button is released, the microcontroller starts executing from address 0 of the program memory.

### 1.4.6 Interrupts

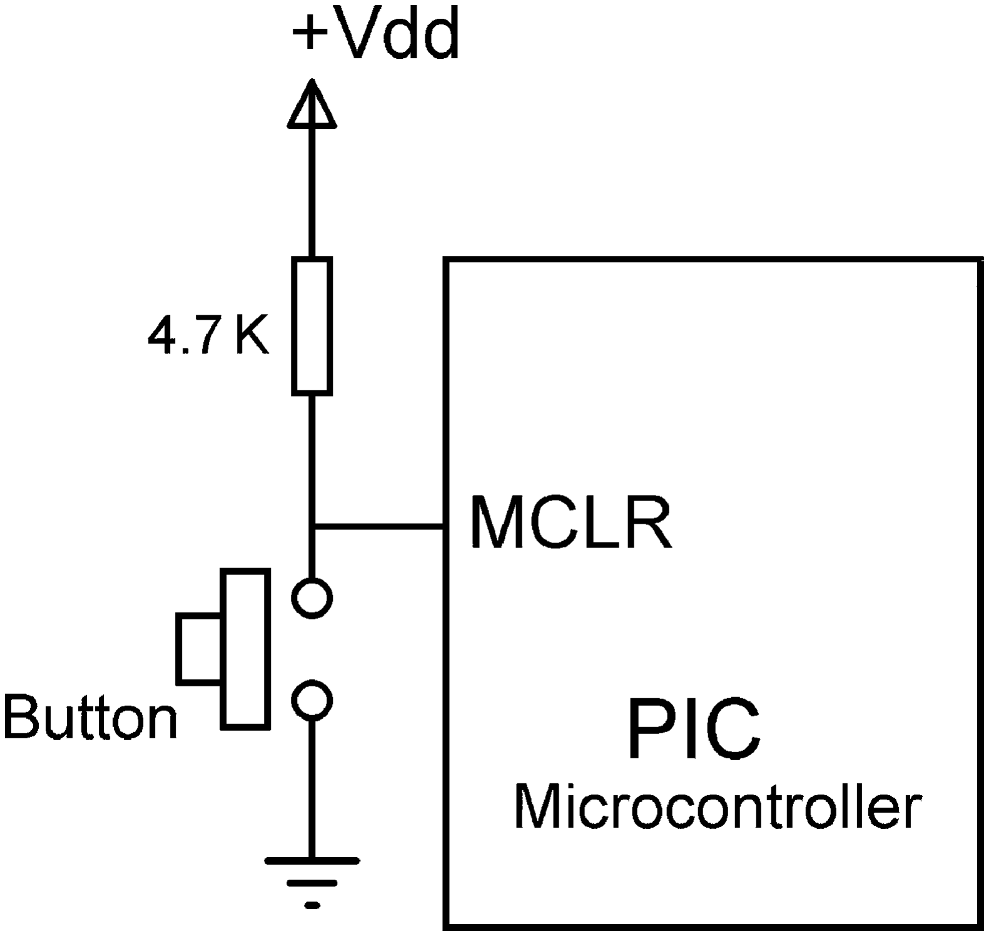
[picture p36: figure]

Interrupts are an important feature of all microcontrollers. An interrupt can either occur asynchronously or synchronously. Asynchronous interrupts are usually external events which interrupt the microcontroller and request service. For example, pin INT (RB0) of a PIC16F84 microcontroller is the external interrupt pin and this pin can be used to interrupt the microcontroller asynchronously; i.e., the interrupt can occur at any time independent of the program being executed inside the microcontroller. Synchronous interrupts are usually timer interrupts, such as the timer overfl ow generating an interrupt.

Depending on the model used, different PIC microcontrollers may have a different number of interrupt sources. For example, the PIC16F84 microcontroller has the following four sources of interrupts:

- External interrupt from INT (RB0) pin
- TMR0 interrupt caused by timer overfl ow
- External interrupt when the state of RB4, RB5, RB6, or RB7 pins change
- Termination of writing data to the EEPROM.

Interrupts are enabled and disabled by the INTCON register. Each interrupt source has two bits to control it. One enables interrupts, and the other one detects when an interrupt occurs. There is a common bit called GIE (see INTCON register bit defi nitions) which can be used to disable all sources of interrupts.

Figure 1.24: Using an External Reset Button

### 32 Chapter 1

The INTCON control bits of various interrupt sources are

Interrupt Source | Enabled by | Completion Status
External interrupt from INT | INTE 1 | INTF 1
TMR0 interrupt | T0IE 1 | T0IF 1
RB4–RB7 state change | RBIE 1 | RBIF 1
EEPROM write complete | EEIE 1 | –

Whenever an interrupt occurs, the microcontroller jumps to the ISR. On low-end microcontrollers (e.g., PIC16F84 or PIC16F628) all interrupt sources use address 4 in program memory as the start of the ISR. Because all interrupts use the same ISR address, we have to check the interrupt completion status to detect which interrupt has occurred when multiple interrupts are enabled.

The completion status has to be cleared to zero if we want the same interrupt source to be able to interrupt again.

Assuming that we wish to use the external interrupt (INT) input, and interrupts should be accepted on the low to high transition of the INT pin, the steps before and after an interrupt are summarized below.

- Set the direction of the external interrupt to be on rising edge by setting INTEDG 1 in register OPTION_REG.
- Enable INT interrupts by setting INTE 1 in register INTCON.
- Enable global interrupts by setting GIE 1 in register INTCON.
- Carry out normal processing. When interrupt occurs, program will jump to the ISR.
- Carry out the required tasks in the ISR routine.
- At the end of the ISR, re-enable the INT interrupts by clearing INTF 0.

### 1.4.7 The Confi guration Word

PIC microcontrollers have a special register called the Confi guration Word. This is a 14-bit register and is mapped in program memory 2007 (hexadecimal). This address is beyond the user program-memory space and cannot be directly accessed in a program. This register can be accessed during the programming of the microcontroller.

The confi guration word stores the following information about a PIC microcontroller:

- Code protection bits: These bits are used to protect blocks of memory so that they cannot be read.
- Power-on timer enable bit.
- Watchdog (WDT) timer enable bit.

The PIC Microcontroller Family 33

- Oscillator selection bits: The oscillator can be selected as XT, HS, LP, RC, or internal (if supported by the microcontroller).

For example, in a typical application we can have the following confi guration word selection during the programming of the microcontroller:

- Code protection OFF
- XT oscillator selection
- WDT disabled
- Power-up timer enables.

### 1.4.8 I/O Interface

A PIC microcontroller port can source and sink 25 mA of current. When sourcing current, the current is fl owing out of the port pin, and when sinking current, the current is fl owing into the pin. When the pin is sourcing current, one pin of the load is connected to the microcontroller port and the other pin to the ground (see Fig. 1.25a). The load is then energized when the port output is at logic 1. When the pin is sinking current, one pin of the load is connected to the supply voltage and the other pin to the output of the port (see Fig. 1.25b). The load is then energized when the port output is at logic 0.

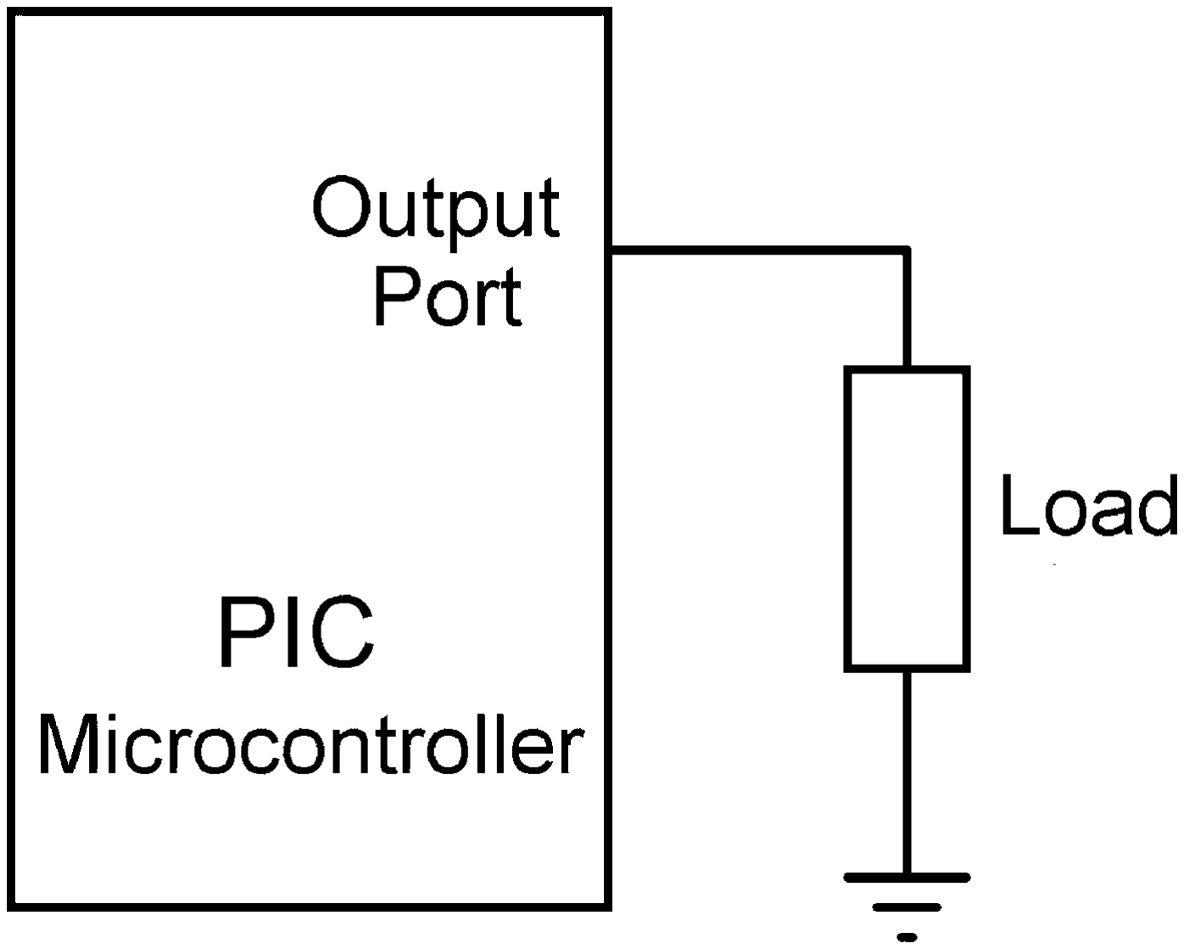
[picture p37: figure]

Figure 1.25a: Current Sourcing

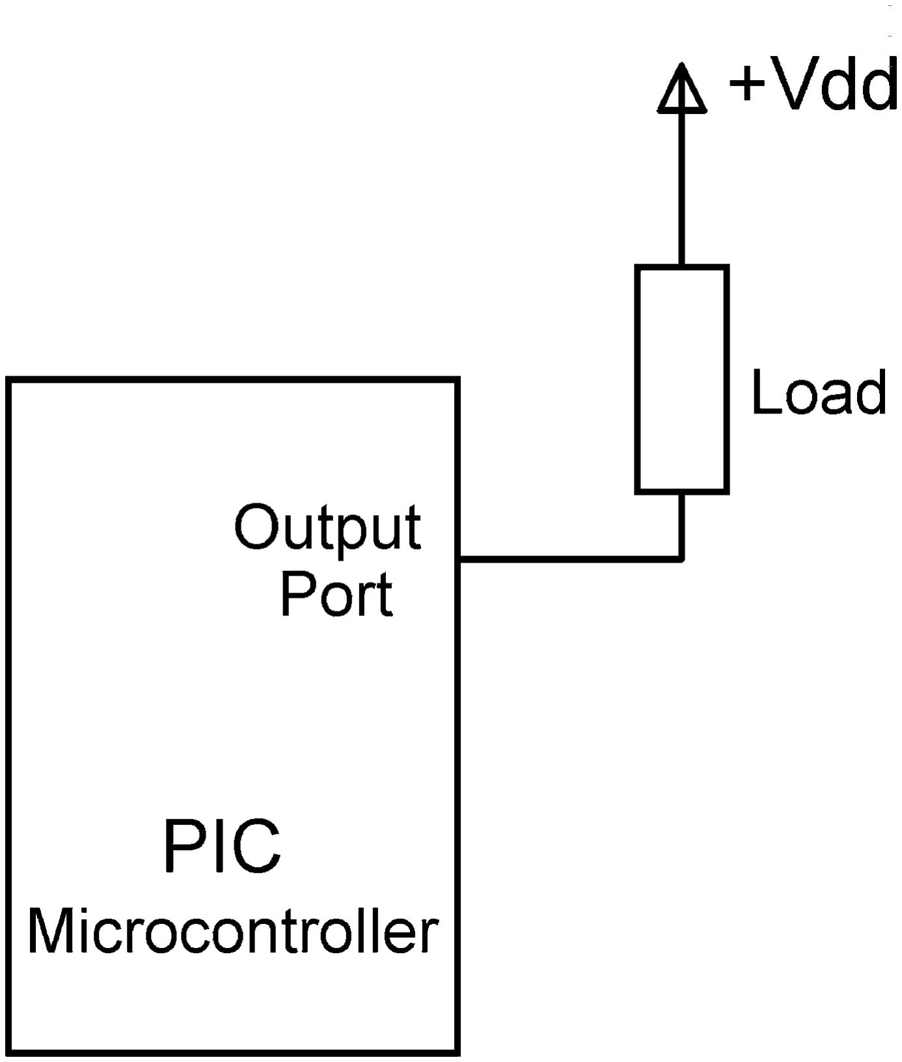
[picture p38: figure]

Figure 1.25b: Current Sinking

Some useful interface circuits are given in this section.

### 34 Chapter 1

### 1.4.8.1 LED Interface

LEDs come in many different sizes, shapes, and colors. The brightness of an LED depends on the current through the device. Some small LEDs operate with only a few milliamperes of current, while standard size LEDs consume about 10 mA of current for normal brightness. Some very bright LEDs consume 15–20 mA of current. The voltage drop across an LED
is about 2 V, but the voltage at the output of a microcontroller port is about 5 V when the port is at logic 1 level. As a result of this, it is not possible to connect an LED directly to a microcontroller output port. What is required is a resistor to limit the current in the circuit.

If the output voltage of the port is 5 V and the voltage drop across the LED is 2 V, we need to drop 3 V across the resistor. If we assume that the current through the LED is 10 mA, we can calculate the value of the required resistor as

R | | 5 | 2V
10 mA

3V
10 mA

0.3 K

The nearest physical resistor we can use is 330 . Figure 1.26 shows how an LED can be connected to an output port pin in current source mode. In this circuit the LED will be ON when the port output is set to logic 1. Similarly, Fig. 1.27 shows how an LED can be connected to an output port pin in current sink mode. In this circuit the LED will be ON when the port output is at logic 0.

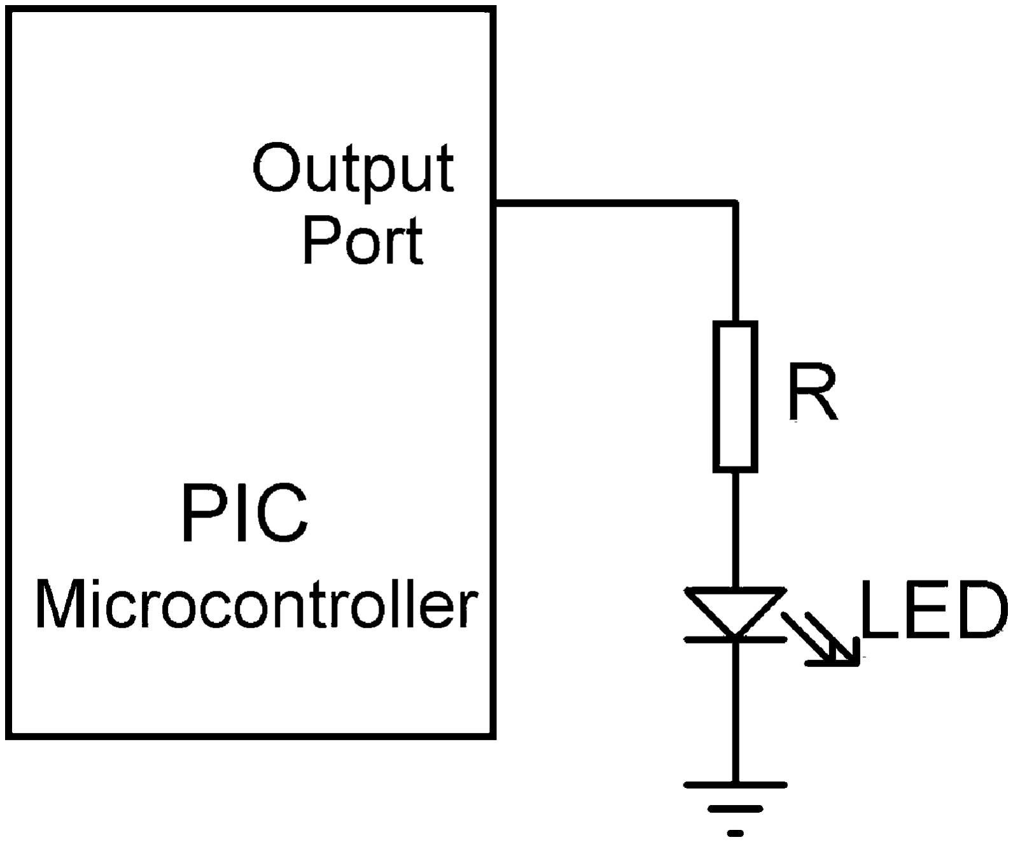
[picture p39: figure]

Figure 1.26: Connecting an LED in Current Source Mode

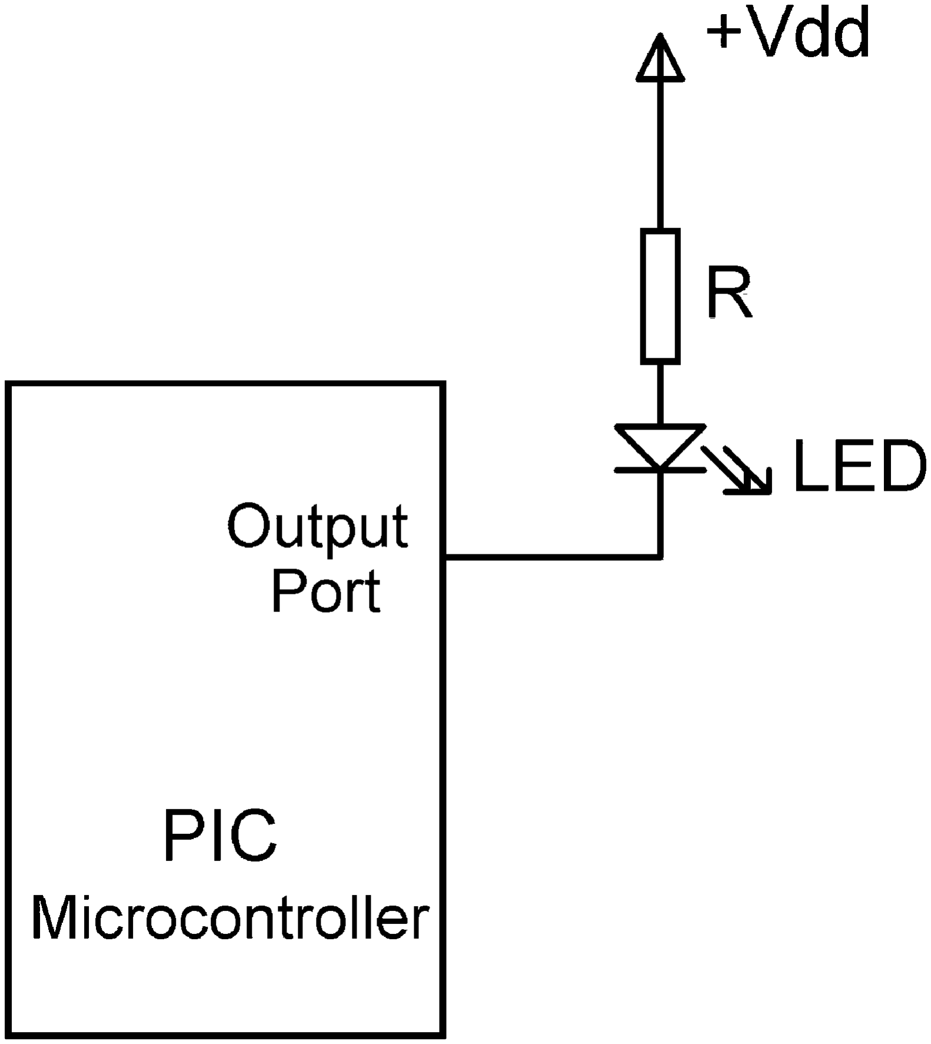
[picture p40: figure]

Figure 1.27: Connecting an LED in Current Sink Mode

The PIC Microcontroller Family 35

### 1.4.8.2 Higher Current Load Interface

The circuits given in Figs 1.26 and 1.27 work fi ne for an LED, or for any other device whose current requirement is less than 25 mA. What do we do if we wish to operate a load with
a higher current rating (e.g., a 12 V fi lament lamp)? The answer is that we have to use a switching device, such as a transistor or a relay.

Figure 1.28 shows how we can drive a small lamp from our port pin using a bipolar transistor. In this circuit, when the port output pin is at logic 1, current fl ows through the resistor and turns the transistor ON, effectively connecting the bottom end of the lamp to ground. It is important to realize that the positive supply to the lamp is not related to the PIC supply voltage and while the PIC is operating from 5 V, the lamp can be operated from a 12 V supply.The current capability depends upon the type of transistor used and several hundred milliamperes can be achieved with any type of small npn transistors. For higher currents, bipolar power transistors, or preferably MOSFET transistors, can be used.

### 1.4.8.3 Relay Interface

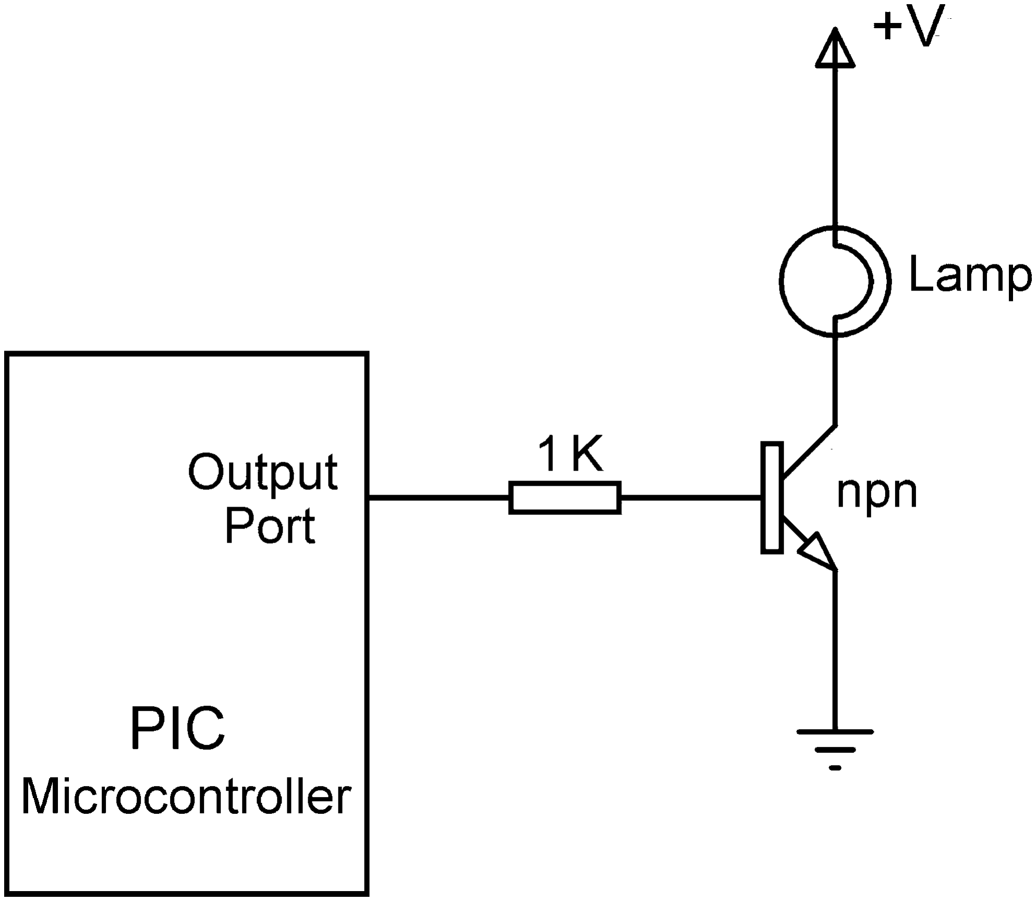
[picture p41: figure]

When we want to switch inductive loads such as relays we have to use a diode in the circuit to prevent the transistor from being damaged (see Fig. 1.29). An inductive load can generate a

Figure 1.28: Driving a Lamp Using a Transistor

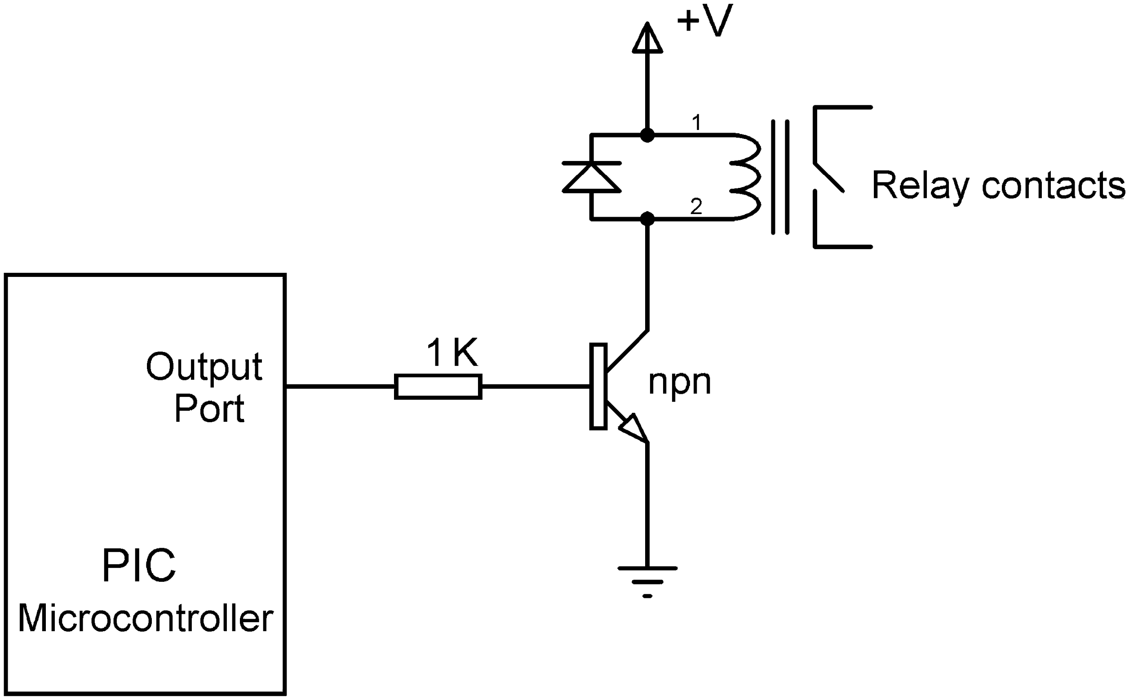
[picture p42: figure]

Figure 1.29: Driving an Inductive Load (e.g., a Relay)

### 36 Chapter 1

back EMF which could easily damage a transistor. By connecting a diode in reverse bias mode this back EMF is dissipated without damaging the transistor.

Since we can drive a relay, we can connect any load to the relay outputs as long as we do not exceed the contact ratings of the relay. Figure 1.30 shows how a mains lamp can be operated from the microcontroller output port using a relay. The relay could also be operated using a MOSFET power transistor. In this circuit the mains lamp will turn ON when the output port of the microcontroller is a logic 1.

### 1.4.8.4 Button Input

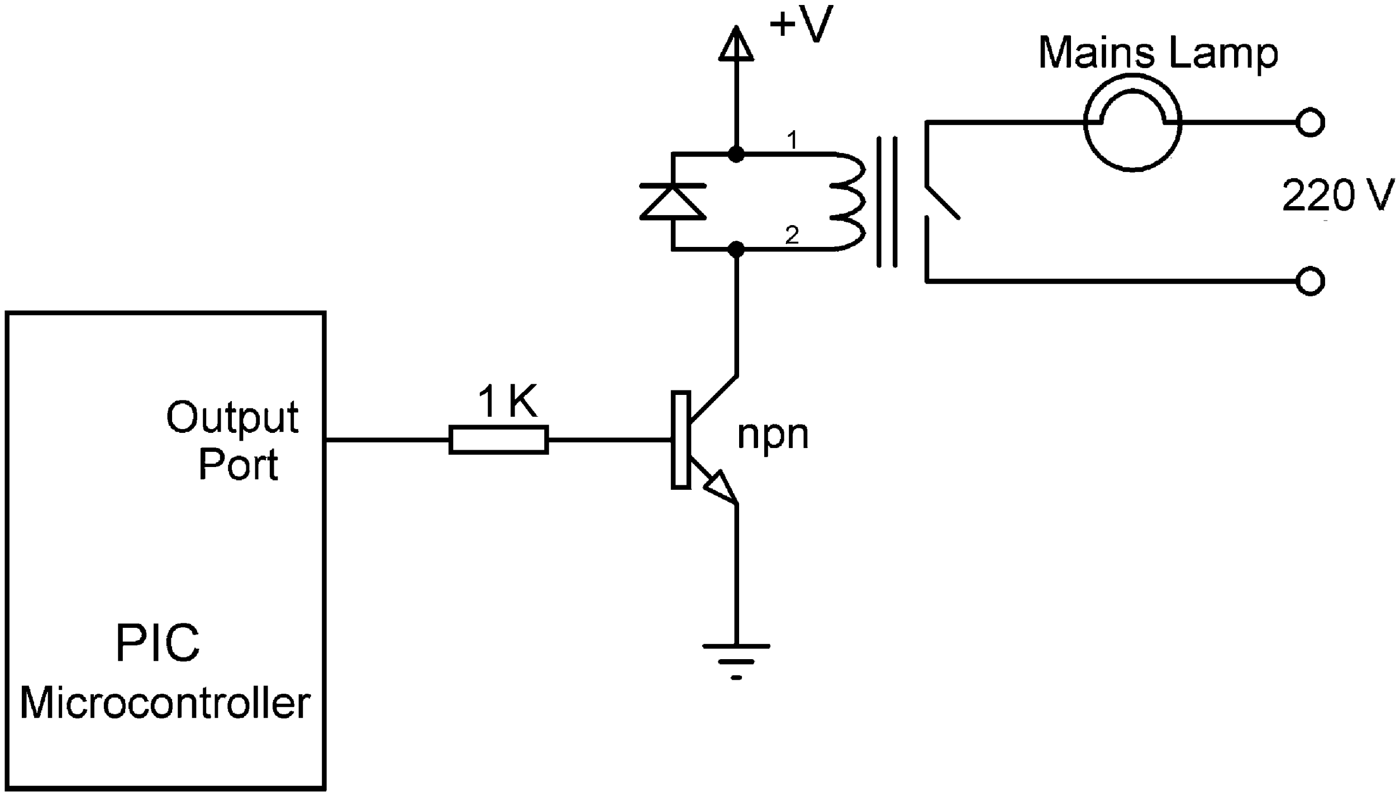
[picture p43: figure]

One of the most common types of inputs is a button (a push-button switch) input where the user can change the state of an input pin by pressing a button. Basically, button input can use two different methods: active low and active high. As shown in Fig. 1.31, in active low implementation, the microcontroller input pin is connected to the supply voltage using a resistor (this is also called a pull-up resistor) and the button is connected between the port pin and ground. Normally the microcontroller input is pulled to logic 1 by the resistor. When the button is pressed, the input is forced to ground potential, which is logic 0. The change of state in the input pin can be determined by a program.

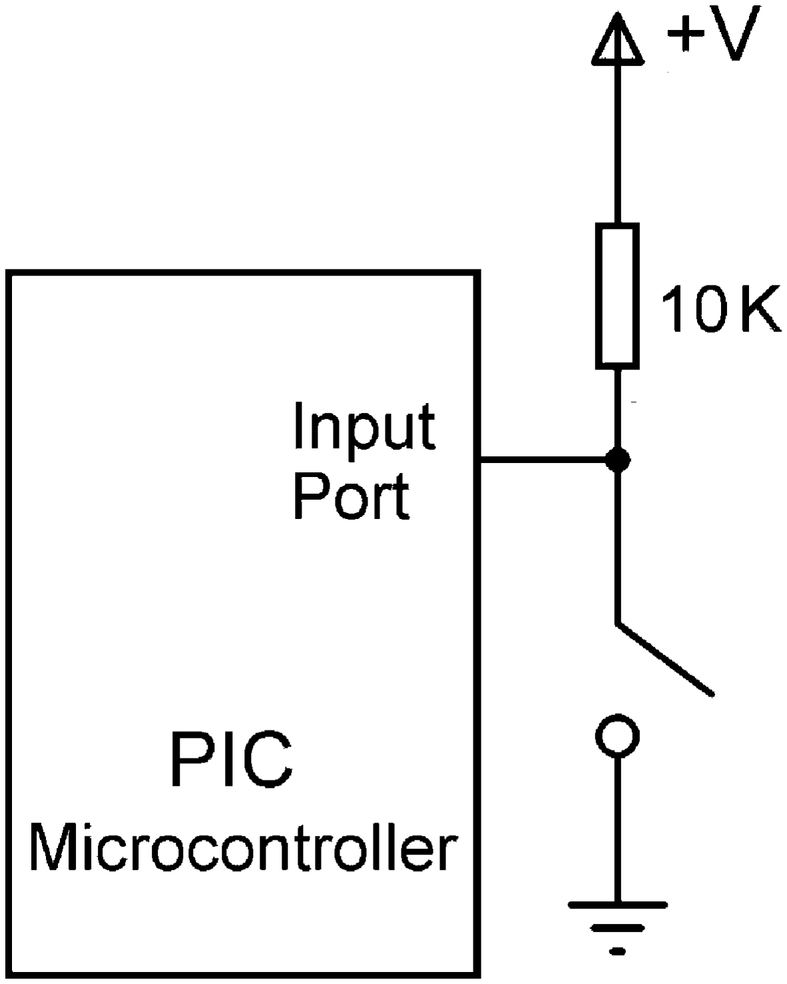
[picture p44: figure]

Figure 1.31: Active Low-Button Input

Figure 1.30: Driving a Mains Bulb Using a Relay

The PIC Microcontroller Family 37

Some ports in PIC microcontrollers have internal pull-up resistors (e.g., PORTB) and these resistors can be enabled by clearing bit 7 (RBPU) of register INTCON to zero. When one of these port pins is used for button input, there is no need to use an external pull-up resistor and the button can simply be connected between the port pin and ground.

A button can also be connected in active high mode as shown in Fig. 1.32. In this confi guration the button is connected between the supply voltage and the port pin. A resistor (this is also called a pull-down resistor) is connected between the port pin and ground. Normally, the port pin is at logic 0. When the button is pressed the port pin goes to the supply voltage, which is logic 1.


One of the problems with mechanical switches is that, when a switch closes, its metal parts compress and relax and this causes the switch to open and close several times quickly. The problem is that the microcontroller can read the switch so fast that it can see the switch open and close during the bouncing of the metal parts and this can cause a wrong switch state to be read by the microcontroller. One way to eliminate this switch-bouncing problem is to delay reading the input after the switch state changes. For example, when we detect the switch is pressed, we may wait about 10 ms before we read the state of the switch.

In Figs 1.31 and 1.32, we have seen how simple buttons can be connected to a micro controller port. It is also possible to connect a switching transistor to an input pin, the output of another IC, or simply the output of another PIC port pin. Figure 1.33 shows how a switching transistor can be connected as an input. In this circuit the transistor acts like an inverting switch. When the transistor input voltage is 0 V, the transistor is in OFF state and the port pin is at logic 1 level. When the transistor input voltage is 5 V the transistor turns ON and its collector-emitter voltage drops to 0 V, making the port pin logic 0. One nice thing about this circuit is that the transistor input voltage does not need to be 5 V to turn the transistor ON; it could easily be
9 or 12 V.

Figure 1.32: Active High-Button Input

### 38 Chapter 1


The input ports of PIC microcontrollers are protected by internal diodes for over-voltage and under-voltage. Thus, the voltage on a pin can exceed the supply voltage, or it can go below the ground voltage, without causing any harm to the microcontroller. The RS232 serial communication lines operate with 12 V and we can usually connect these lines directly to the input ports using resistors without damaging the microcontroller.

Figure 1.33: Transistor Input

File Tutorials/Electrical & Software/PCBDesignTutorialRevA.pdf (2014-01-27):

# PCB Design Tutorial


# by David L. Jones

### Email: david AT alternatezone DOT com

## Revision A - June 29th 2004

### The latest version of this tutorial can be found through www.alternatezone.com

Freely distributable for educational and personal use. Copyright© 2004 David L. Jones

PCB Design Tutorial by David L. Jones

Page 2 of 25 2

Page 3 of 25 3

## Introduction

You've designed your circuit, perhaps even bread boarded a working prototype, and now it's time to turn it into a nice Printed Circuit Board (PCB) design. For some designers, the PCB design will be a natural and easy extension of the design process. But for many others the process of designing and laying out a PCB can be a very daunting task. There are even very experienced circuit designers who know very little about PCB design, and as such leave it up to the "expert" specialist PCB designers. Many companies even have their own dedicated PCB design departments. This is not surprising, considering that it often takes a great deal of knowledge and talent to position hundreds of components and thousands of tracks into an intricate (some say artistic) design that meets a whole host of physical and electrical requirements. Proper PCB design is very often an integral part of a design. In many designs (high speed digital, low level analog and RF to name a few) the PCB layout may make or break the operation and electrical performance of the design. It must be remembered that PCB traces have resistance, inductance, and capacitance, just like your circuit does.
This article is presented to hopefully take some of the mystery out of PCB design. It gives some advice and “rules of thumb” on how to design and lay out your PCBs in a professional manner. It is, however, quite difficult to try and “teach” PCB design. There are many basic rules and good practices to follow, but apart from that PCB design is a highly creative and individual process. It is like trying to teach someone how to paint a picture. Everyone will have their own unique style, while some people may have no creative flair at all!
Indeed, many PCB designers like to think of PCB layouts as works of art, to be admired for their beauty and elegance. “If it looks good, it’ll work good.” is an old catch phrase.
Lets have a go shall we...

## The Old Days

Back in the pre-computer CAD days, PCBs were designed and laid out by hand using adhesive tapes and pads on clear drafting film. Many hours were spent slouched over a fluorescent light box, cutting, placing, ripping up, and routing tracks by hand. Bishop Graphics, Letraset, and even Dalo pens will be names that evoke fond, or not so fond memories. Those days are well and truly gone, with computer based PCB design having replaced this method completely in both hobbyist and professional electronics. Computer based CAD programs allow the utmost in flexibility in board design and editing over the traditional techniques. What used to take hours can now be done in seconds.

## PCB Packages

There are many PCB design packages available on the market, a few of which are freeware, shareware, or limited component full versions. Protel is the defacto industry standard package in Australia. Professionals use the expensive high end Windows based packages such as 99SE and DXP. Hobbyists use the excellent freeware DOS based Protel AutoTrax program, which was, once upon a time, the high-end package of choice in Australia. Confusingly, there is now another Windows based package also called AutoTrax EDA. This is in no way related to the Protel software.
This article does not focus on the use of any one package, so the information can be applied to almost any PCB package available. There is however, one distinct exception. Using a PCB only package, which does not have schematic capability, greatly limits what you can do with the package in the professional sense. Many of the more advanced techniques to be described later require access to a compatible schematic editor program. This will be explained when required.

## Standards

There are industry standards for almost every aspect of PCB design. These standards are controlled by the former Institute for Interconnecting and Packaging Electronic Circuits, who are now known simply as the IPC (www.ipc.org). There is an IPC standard for every aspect of PCB design, manufacture, testing, and anything else that you could ever need. The major document that covers PCB design is IPC-2221, “Generic Standard on

Page 4 of 25 4

Printed Board Design”. This standard superseded the old IPC-D-275 standard (also Military Std 275) which has been used for the last half century.
Local countries also have their own various standards for many aspects of PCB design and manufacture, but by and large the IPC standards are the accepted industry standard around the world.
Printed Circuit Boards are also known (some would say, more correctly known) as Printed Wiring Boards, or simply Printed Boards. But we will settle on the more common term PCB for this article.

## The Schematic

Before you even begin to lay out your PCB, you MUST have a complete and accurate schematic diagram. Many people jump straight into the PCB design with nothing more than the circuit in their head, or the schematic drawn on loose post-it notes with no pin numbers and no order. This just isn’t good enough, if you don’t have an accurate schematic then your PCB will most likely end up a mess, and take you twice as long as it should. “Garbage-in, garbage-out” is an often used quote, and it can apply equally well to PCB design. A PCB design is a manufactured version of your schematic, so it is natural for the PCB design to be influenced by the original schematic. If your schematic is neat, logical and clearly laid out, then it really does make your PCB design job a lot easier. Good practice will have signals flowing from inputs at the left to outputs on the right. With electrically important sections drawn correctly, the way the designer would like them to be laid out on the PCB. Like putting bypass capacitors next to the component they are meant for. Little notes on the schematic that aid in the layout are very useful. For instance, “this pin requires a guard track to signal ground”, makes it clear to the person laying out the board what precautions must be taken. Even if it is you who designed the circuit and drew the schematic, notes not only remind yourself when it comes to laying out the board, but they are useful for people reviewing the design.
Your schematic really should be drawn with the PCB design in mind.
It is outside the scope of this article to go into details on good schematic design, as it would require a complete article in its own right.

## Imperial and Metric

The first thing to know about PCB design is what measurement units are used and their common terminologies, as they can be awfully confusing!
As any long time PCB designer will tell you, you should always use imperial units (i.e. inches) when designing PCBs. This isn’t just for the sake of nostalgia, although that is a major reason! The majority of electronic components were (and still are) manufactured with imperial pin spacing. So this is no time to get stubborn and refuse to use anything but metric units, metric will make laying out of your board a lot harder and a lot messier. If you are young enough to have been raised in the metric age then you had better start learning what inches are all about and how to convert them.
An old saying for PCB design is “thou shall use thous”. A tad confusing until you know what a “thou” is.
A “thou” is 1/1000th of an inch, and is universally used and recognised by PCB designers and manufacturers everywhere. So start practicing speaking in terms of “10 thou spacing” and “25 thou grid”, you’ll sound like a professional in no time!
Now that you understand what a thou is, we’ll throw another spanner in the works with the term “mil” (or “mils”). 1 “mil” is the same as 1 thou, and is NOT to be confused with the millimeter (mm), which is often spoken the
same as “mil”. The term “mil” comes from 1 thou being equal to 1 mili inch. As a general rule avoid the use of “mil” and stick to “thou”, it’s less confusing when trying to explain PCB dimensions to those metricated non-PCB people.
Some PCB designers will tell you not to use metric millimeters for ANYTHING to do with a PCB design. In the practical world though, you’ll have to use both imperial inches (thous) and the metric millimeter (mm). So which units do you use for what? As a general rule, use thous for tracks, pads, spacings and grids, which are most of your basic “design and layout” requirements. Only use mm for “mechanical and manufacturing” type requirements like hole sizes and board dimensions.

Page 5 of 25 5

You will find that many PCB manufacturers will follow these basic guidelines also, for when they ask you to provide details for a quote to manufacture your board. Most manufacturers use metric size drills, so specifying imperial size holes really is counterproductive and can be prone to errors.
Just to confuse the issue even further, there are many components (new surface mount parts are an example) which have metric pin spacing and dimensions. So you’ll often have to design some component footprints using metric grids and pads. Many component datasheets will also have metric dimensions even though the spacing are designed to an imperial grid. If you see a “weird” metric dimension like 1.27mm in a component, you can be pretty sure it actually has a nice round imperial equivalent. In this case 1.27mm is 50 thou.
Yes, PCB design can be confusing!
So whatever it is you have to do in PCB design you’ll need to become an expert at imperial to metric conversion, and vice-versa. To make your life easier though, all the major PCB drafting packages have a single “hot key” to convert between imperial and metric units instantly (“Q” on Protel for instance). It will help you greatly if you memorise a few key conversions, like 100 thou (0.1 inch) = 2.54mm, and 200 thou (0.2 inch) = 5.08mm etc Values of 100 thou and above are very often expressed in inches instead of thous. So 0.2 inch is more
commonly used than 200thou.
1 inch is also commonly known as 1 “pitch”. So it is common to hear the phrase “0.1 inch pitch”, or more simply “0.1 pitch” with the inches units being assumed. This is often used for pin spacing on components.
100 thou is a basic “reference point” for all aspects of PCB design, and a vast array of common component lead spacing are multiples or fractions of this basic unit. 50 and 200 thou are the most common.
Along with the rest of the world, the IPC standards have all been metricated, and only occasionally refer to imperial units. This hasn’t really converted the PCB industry though. Old habits die hard, and imperial still reigns supreme in many areas of practical usage.

## Working to Grids

The second major rule of PCB design, and the one most often missed by beginners, is to lay out your board on a fixed grid. This is called a “snap grid”, as your cursor, components and tracks will “snap” into fixed grid positions. Not just any size grid mind you, but a fairly coarse one. 100 thou is a standard placement grid for very basic through hole work, with 50 thou being a standard for general tracking work, like running tracks between through-hole pads. For even finer work you may use a 25 thou snap grid or even lower. Many designers will argue over the merits of a 20 thou grid vs a 25 thou grid for instance. In practice, 25 thou is often more useful as it allows you to go exactly half way between 50 thou spaced pads.
Why is a coarse snap grid so important? It’s important because it will keep your components neat and symmetrical; aesthetically pleasing if you may. It’s not just for aesthetics though - it makes future editing, dragging, movement and alignment of your tracks, components and blocks of components easier as your layout grows in size and complexity.
A bad and amateurish PCB design is instantly recognisable, as many of the tracks will not line up exactly in the center of pads. Little bits of tracks will be “tacked” on to fill in gaps etc. This is the result of not using a snap grid effectively.
Good PCB layout practice would involve you starting out with a coarse grid like 50 thou and using a progressively finer snap grid if your design becomes “tight” on space. Drop to 25 thou and 10 thou for finer routing and placement when needed. This will do 99% of boards. Make sure the finer grid you choose is a nice even division of your standard 100 thou. This means 50, 25, 20, 10, or 5 thou. Don’t use anything else, you’ll regret it.
A good PCB package will have hotkeys or programmable macro keys to help you switch between different snap grid sizes instantly, as you will need to do this often.
There are two types of grids in a PCB drafting package, a snap grid as discussed, and a “visible” grid. The visible grid is an optional on-screen grid of solid or dashed lines, or dots. This is displayed as a background behind your design and helps you greatly in lining up components and tracks. You can have the snap grid and visible grid set to different units (metric or imperial), and this is often very helpful. Many designers prefer a 100 thou visible grid and rarely vary from that.

Page 6 of 25 6

Some programs also have what is called an “Electrical” grid. This grid is not visible, but it makes your cursor “snap” onto the center of electrical objects like tracks and pads, when your cursor gets close enough. This is extremely useful for manual routing, editing and moving objects.
One last type of grid is the “Component” grid. This works the same as the snap grid, but it’s for component movement only. This allows you to align components up to a different grid. Make sure you make it a multiple of your Snap grid.
When you start laying out your first board, snap grids can feel a bit “funny”, with your cursor only being able to be moved in steps. Unlike normal paint type packages which everyone is familiar with. But it’s easy to get used to, and your PCB designs will be one step closer to being neat and professional.

## Working from the top

PCB design is always done looking from the top of your board, looking through the various layers as if they were transparent. This is how all the PCB packages work. The only time you will look at your board from the bottom is for manufacturing or checking purposes. This “through the board” method means that you will have to get used to reading text on the bottom layers as a mirror image, get used to it!

## Tracks

There is no recommended standard for track sizes. What size track you use will depend upon (in order of importance) the electrical requirements of the design, the routing space and clearance you have available, and your own personal preference. Every design will have a different set of electrical requirements which can vary between tracks on the board. All but basic non-critical designs will require a mixture of track sizes. As a general rule though, the bigger the track width, the better. Bigger tracks have lower DC resistance, lower inductance, can be easier and cheaper for the manufacturer to etch, and are easier to inspect and rework.
The lower limit of your track width will depend upon the “track/space” resolution that your PCB manufacturer is capable of. For example, a manufacturer may quote a 10/8 track/space figure. This means that tracks can be no less than 10 thou wide, and the spacing between tracks (or pads, or any part of the copper) can be no less than 8 thou. The figures are almost always quoted in thou’s, with track width first and then spacing.
Real world typical figures are 10/10 and 8/8 for basic boards. The IPC standard recommends 4thou as being a lower limit. Once you get to 6thou tracks and below though, you are getting into the serious end of the business, and you should be consulting your board manufacturer first. The lower the track/space figure, the greater care the manufacturer has to take when aligning and etching the board. They will pass this cost onto you, so make sure that you don’t go any lower than you need to. As a guide, with “home made” PCB manufacturing processes like laser printed transparencies and pre-coated photo resist boards, it is possible to easily get 10/10 and even 8/8 spacing.
Just because a manufacturer can achieve a certain track/spacing, it is no reason to “push the limits” with your design. Use as big a track/spacing as possible unless your design parameters call for something smaller.
As a start, you may like to use say 25 thou for signal tracks, 50 thou for power and ground tracks, and 10-15 thou for going between IC and component pads. Some designers though like the “look” of smaller signal tracks like 10 or 15 thou, while others like all of their tracks to be big and “chunky”. Good design practice is to keep tracks as big as possible, and then to change to a thinner track only when required to meet clearance requirements.
Changing your track from large to small and then back to large again is known as
“necking”, or “necking down”. This is often required when you have to go between IC
or component pads. This allows you to have nice big low impedance tracks, but still
have the flexibility to route between tight spots.
In practice, your track width will be dictated by the current flowing through it, and the maximum temperature rise of the track you are willing to tolerate. Remember that every track will have a certain amount of resistance, so the track will dissipate heat just like a resistor. The wider the track the lower the resistance. The thickness of the copper on your PCB will also play a part, as will any solder coating finish.

Page 7 of 25 7

The thickness of the copper on the PCB is nominally specified in ounces per square foot, with 1oz copper being the most common. You can order other thicknesses like 0.5oz, 2oz and 4oz. The thicker copper layers are useful for high current, high reliability designs.
The calculations to figure out a required track width based on the current and the maximum temperature rise are a little complex. They can also be quite inaccurate, as the standard is based on a set of non-linear graphs based on measured data from around half a century ago. These are still reproduced in the IPC standard.
A handy track width calculator program can be found at www.ultracad.com/calc.htm, and gives results based on the IPC graphs.
As a rule of thumb, a 10degC temperature rise in your track is a nice safe limit to design around. A handy reference table has been included in this article to give you a list of track widths vs current for a 10degC rise. The DC resistance in milli ohms per inch is also shown. Of course, the bigger the track the better, so don’t just blindly stick to the table.

Track Width Reference Table (for 10deg C temp rise). Track Width is in Thous (mils)
Current (Amps) | Width for 1oz | Width for 2 oz | milli Ohms/Inch
1 | 10 | 5 | 52
2 | 30 | 15 | 17.2
3 | 50 | 25 | 10.3
4 | 80 | 40 | 6.4
5 | 110 | 55 | 4.7
6 | 150 | 75 | 3.4
7 | 180 | 90 | 2.9
8 | 220 | 110 | 2.3
9 | 260 | 130 | 2.0
10 | 300 | 150 | 1.7

## Pads

Pad sizes, shapes and dimensions will depend not only upon the component you are using, but also the manufacturing process used to assemble the board, among other things. There are a whole slew of standards and theories behind pad sizes and layouts, and this will be explained later. Suffice it to say at this stage that your PCB package should come with a set of basic component libraries that will get you started. For all but the simplest boards though, you’ll have to modify these basic components to suit your purpose. Over time you will build up your own library of components suitable for various requirements.
There is an important parameter known as the pad/hole ratio. This is the ratio of the pad size to the hole size. Each manufacturer will have their own minimum specification for this. As a simple rule of thumb, the pad should be at least 1.8 times the diameter of the hole, or at least 0.5mm larger. This is to allow for alignment tolerances on the drill and the artwork on top and bottom layers. This ratio gets more important the smaller the pad and hole become, and is particularly relevant to vias.
There are some common practices used when it comes to generic component pads. Pads for leaded components like resistors, capacitors and diodes should be round, with around 70 thou diameter being common. Dual In Line (DIL) components like IC’s are better suited with oval shaped pads (60 thou high by 90-100 thou wide is common). Pin 1 of the chip sould always be a different pad shape, usually rectangular, and with the
same dimensions as the other pins.
Most surface mount components use rectangular pads, although surface mount SO package ICs should use oval pads. Again, with pin 1 being rectangular.
Other components that rely on pin numbering, like connectors and SIP resistor packs, should also follow the “rectangular pin 1” rule.


Page 8 of 25 8

Octagonal pads are seldom used, and should generally be avoided.
As a general rule, use circular or oval pads unless you need to use rectangular.

## Vias

Vias connect the tracks from one side of your board to another, by way of a hole in your board. On all but cheap home made and low end commercial prototypes, vias are made with electrically plated holes, called Plated Through Holes (PTH). Plated through holes allow electrical connection between different layers on your board. What is the difference between a via and a pad? Practically speaking there is no real difference, they are both just electrically plated holes. But there are differences when it comes to PCB design packages. Pads and Vias are, and should be, treated differently. You can globally edit them separately, and do some more advanced things to be discussed later. So don’t use a pad in place of a via, and vice-versa.
Holes in vias are usually a fair bit smaller than component pads, with 0.5-0.7mm being typical.
Using a via to connect two layers is commonly called “stitching”, as you are effectively electrically stitching both layers together, like threading a needle back and forth through material. Throw the term stitching a few times into a conversation and you’ll really sound like a PCB professional!

## Polygons

“Polygons” are available on many PCB packages. A polygon automatically fills in (or “floods”) a desired area with copper, which “flows” around other pads and tracks. They are very useful for laying down ground planes. Make sure you place polygons after you have placed all of your tacks and pads.
Polygon can either be “solid” fills of copper, or “hatched” copper tracks in a crisscross fashion. Solid fills are preferred, hatched fills are basically a thing of the past.

An example of a “Solid Polygon Fill” (Left), and a “Hatched Polygon Fill” (Right)

## Clearances

Electrical clearances are an important requirement for all boards. Too tight a clearance between tracks and pads may lead to “hairline” shorts and other etching problems during the manufacturing process. These can be very hard to fault find once your board is assembled. Once again, don’t “push the limits” of your manufacturer unless you have to, stay above their recommended minimum spacing if at all possible.
At least 15 thou is a good clearance limit for basic through hole designs, with 10 thou or 8 thou being used for more dense surface mount layouts. If you go below this, it’s a good idea to consult with your PCB manufacturer first.
For 240V mains on PCB’s there are various legal requirements, and you’ll need to consult the relevant standards if you are doing this sort of work. As a rule of thumb, an absolute minimum of 8mm (315 thou) spacing should be allowed between 240V tracks and isolated signal tracks. Good design practice would dictate that you would have much larger clearances than this anyway.
For non-mains voltages, the IPC standard has a set of tables that define the clearance required for various voltages. A simplified table is shown here. The clearance will vary depending on whether the tracks are on an internal layers or the external surface. They also vary with the operational height of the board above sea level,

Page 9 of 25 9

due to the thinning of the atmosphere at high altitudes. Conformal coating also improves these figures for a given clearance, and this is often used on military spec PCBs.

### Clearances for Electrical Conductors

Voltage (DC or Peak AC) | Internal | External (<3050m) | External (>3050m)
0-15V | 0.05mm | 0.1mm | 0.1mm
16-30V | 0.05mm | 0.1mm | 0.1mm
31-50V | 0.1mm | 0.6mm | 0.6mm
51-100V | 0.1mm | 0.6mm | 1.5mm
101-150V | 0.2mm | 0.6mm | 3.2mm
151-170V | 0.2mm | 1.25mm | 3.2mm
171-250V | 0.2mm | 1.25mm | 6.4mm
251-300V | 0.2mm | 1.25mm | 12.5mm
301-500V | 0.25mm | 2.5mm | 12.5mm

## Component Placement & Design

An old saying is that PCB design is 90% placement and 10% routing. Whilst the actual figures are of no importance, the concept that component placement is by far the most important aspect of laying out a board certainly holds true. Good component placement will make your layout job easier and give the best electrical performance. Bad component placement can turn your routing job into a nightmare and give poor electrical performance. It may even make your board unmanufacturable. So there is a lot to think about when placing components!
Every designer will have their own method of placing components, and if you gave the same circuit (no matter how simple) to 100 different experienced designers you’d get a 100 different PCB layouts every time. So there is no absolute right way to place your components. But there are quite a few basic rules which will help ease your routing, give you the best electrical performance, and simplify large and complex designs.
At this point it is a good idea to give you an idea of the basic steps required to go about laying out a complete board:
ÿ Set your snap grid, visible grid, and default track/pad sizes.
ÿ Throw down all the components onto the board.
ÿ Divide and place your components into functional “building blocks” where possible. ÿ Identify layout critical tracks on your circuit and route them first.
ÿ Place and route each building block separately, off the board.
ÿ Move completed building blocks into position on your main board.
ÿ Route the remaining signal and power connections between blocks. ÿ Do a general “tidy up” of the board.
ÿ Do a Design Rule Check.
ÿ Get someone to check it

This is by no means a be-all and end-all check list, it’s highly variable depending on many factors. But it is a good general guide to producing a professional first-class layout.

Lets look in more detail at the procedure described above.

Page 10 of 25 10

We have already looked at the grids and track/pad sizes, these should be the first things that you set up before you start doing anything. No exceptions!
Many people like to jump straight into placing all the components into what they think is the most optimum position on the board, all in one hit. Whilst this can work for small circuits, you don’t have much of a hope when you have more complex circuits with hundreds of components spread across many functional circuit blocks. Why?, because it’s very easy to run out of “routing space”, which is the room to lay down all your tracks. If you fix all your component positions and then try to route everything, you can easily paint yourself into a corner so to speak. Alternatively, if you space the components out too much, you can end up with a large board that does not make efficient use of space.
The hallmark of an inexperienced designer is a board that has every component evenly spaced out, and then has thousands of tracks and vias crisscrossing the board. It might work, but it can be ugly and inefficient, not to mention bigger and more expensive to manufacture.
The best way to start your layout is to get ALL of your components onto the screen first.
If you have a companion schematic package, then the simplest way to do this is to get your PCB program to import your schematic design and select all the components automatically. This will also be discussed later. If all you have is a PCB program, then you’ll have to select each component from the library and place them down manually.
With all the components on screen, you should get a good indication of whether or not your parts will easily fit onto the size (and shape) of board that you require. If it looks like it’s going to be a tight fit then you know that you will have to work hard to try and keep the component spacing “tight”, and the tracking as efficient as possible. If it looks like you have plenty of room then you can be a bit more liberal in your layout. Of course, if it looks like you have buckleys chance of getting your components on the board, you’ll have to go back to the drawing board.
Now analyse your schematic and determine which parts of the design can be broken up into “building blocks”. Often this is fairly obvious. Say for example you have a complex looking active filter in your circuit. This would typically have a single input line and a single output line, but it will have lots of components and connections as part of the filter. This is a classic “building block” circuit, and one that lends itself well to combining all of these parts together in the same location. So you would grab all of these parts and start to rearrange them into their own little layout off to one side of your board. Don’t worry too much about where the actual block goes on your board yet.
You will also need to partition off electrically sensitive parts of your design into bigger blocks. One major example is with mixed digital and analog circuits. Digital and analog just do not mix, and will need to be physically and electrically separated. Another example is with high frequency and high current circuits, they do not mix with low frequency and low current sensitive circuits. More about this later.
As a general rule, your components should be neatly lined up. Having ICs in the same direction, resistors in neat columns, polarised capacitors all around the same way, and connectors on the edge of the board. Don’t do this at the expense of having an electrically poor layout, or an overly big board though. Electrical parameters should always take precedence over nicely lined up components.
Symmetry is really nice in PCB design, it’s aesthetically pleasing and just “looks right”. If you have something like two identical building block circuits side by side, and one is laid out slightly differently, it sticks out like a sore thumb.
If you have placed your components wisely, 90% of your work will be done. The last 10% should just be joining the dots so to speak. Well, not quite, but good placement is a good majority of your work done.
Once you are happy with the component placements, you can start to route all the different building blocks separately. When finished, it is then often a simple matter to move and arrange the building blocks into the rest of your design.
The Design Rule Check (DRC) will be covered later, but it is an essential step to ensuring that your board is correct before manufacture. A DRC basically checks for correct connectivity of your tracks, and for correct widths and clearances.
Getting someone to check your board may sound like an overly bureaucratic process, but it really is a vital step. No matter how experienced you are at PCB design, there will always be something you overlooked. A fresh pair of eyes and a different mindset will pick up problems you would never see.
If you don’t have anyone to check your board over and don’t have DRC capability, then you’ll have to do it yourself. Get a printout of your schematic and a highlighter pen. Now, compare every single electrical “net”

Page 11 of 25 11

connection on your board with the schematic, net by net. Highlight each net on the schematic as you complete it. When you are finished, there should be no electrical connections left that aren’t highlighted. You can now be fairly confident that your board is electrically correct.

## Basic Routing

Now it’s time for some basic routing rules. Routing is also known as “tracking”.
Routing is the process of laying down tracks to connect components on your board. An electrical connection between two or more pads is known as a “net”.
ÿ Keep nets as short as possible. The longer your total track length, the greater it’s resistance, capacitance and inductance. All of which can be undesirable factors.
ÿ Tracks should only have angles of 45 degrees. Avoid the use of right angles, and under no circumstances use an angle greater than 90 degrees. This is important to give a professional and neat appearance to your board. PCB packages will have a mode to enforce 45 degree movements, make use of it. There should never be a need to turn it off. Contrary to popular belief, sharp right angle corners on tracks don’t produce measurable EMI or other problems. The reasons to avoid right angles are much simpler - it just doesn’t look good, and it may have some manufacturing implications.
ÿ Forget nice rounded track corners, they are harder and slower to place and have no real advantage. Stick to 45 degree increments. Rounded track bends belong to the pre-CAD taped artwork era.
ÿ “Snake” your tracks around the board, don’t just go “point to point”. Point to point tracking may look more efficient to a beginner at first, but there are a few reasons you shouldn’t use it. The first is that it’s ugly, always an important factor in PCB design! The second is that it is not very space efficient when you want to run more tracks on other layers.
ÿ Enable your Electrical grid, which is sometimes referred to as a “snap to center” or “snap to nearest” option. Let the software find the centers of pads and ends of tracks automatically for you. This is great for when you have pads and tracks which aren’t lined up to your current snap grid. If you don’t have these options enabled then you may have to keep reducing your snap grid until you find one that fits. Far more trouble than it’s worth. There is almost never a reason to have these options disabled.
ÿ Always take your track to the center of the pad, don’t make your track and pad “just touch”. There are few reasons for this. The first is that it’s sloppy and unprofessional. The second is that your program may not think that the track is making electrical connection to the pad. Proper use of a snap grid and electrical grid will avoid problems here.
ÿ Use a single track, not multiple tracks tacked together end to end. It may make no difference to the look of your final board, but it can be a pain for future editing. Often you’ll have to extend a track a bit. In this case it’s best to delete the old one and place a new one. It may take a few extra seconds, but it’s worth it. People looking at your finished board may not know, but YOU’LL know! It’s the little touches like this that set good PCB designers apart.
ÿ Make sure your tracks go right through the exact center of pads and components, and not off to one side. Use of the correct snap grid will ensure that you get this right every time. If your track doesn’t go through the exact center then you are using the wrong snap grid. Why do you need to do this? It makes your board neater and more symmetrical, and it gives you the most clearance.
ÿ Only take one track between 100 thou pads unless absolutely necessary. Only on large and very dense designs should you consider two tracks between pads. Three tracks between pads is not unheard of, but we are talking seriously fine tolerances here.
ÿ For high currents, use multiple vias when going between layers. This will reduce your track impedance and improve the reliability. This is a general rule whenever you need to decrease the impedance of your track or power plane.
ÿ Don’t “drag” tracks to angles other than 45 degrees
ÿ “Neck down” between pads where possible. Eg, a 10 thou track through two 60 thou pads gives a generous 15 thou clearance between track and pad.
ÿ If your power and ground tracks are deemed to be critical, then lay them down first. Also, make your power tracks as BIG as possible.


Page 12 of 25 12

ÿ Keep power and ground tracks running in close proximity to each other if possible, don’t send them in opposite directions around the board. This lowers the loop inductance of your power system, and allows for effective bypassing.
ÿ Keep things symmetrical. Symmetry in tracking and component placement is really nice from a professional aesthetics point of view.
ÿ Don’t leave any unconnected copper fills (also called “dead copper”), ground them or take them out.

If you are laying out a non-plated through double sided board, then there are some additional things to watch out for. Non-plate through holes require you to solder a link through the board on both the top and bottom layer.
- Do not place vias under components. Once the component is soldered in place you won’t be able to access the joint to solder a feed through. The solder joint for the feed through can also interfere with the compnent.
- Try and use through hole component legs to connect top tracks to bottom tracks. This minimises the number of vias. Remember that each via adds two solder joints to your board. The more solder joints you have, the less reliable your board becomes. Not to mention that that it takes a lot longer to assemble.


An example of GOOD power routing (Left) and BAD power routing (Right)

An example of GOOD routing (Left) and BAD routing (Right)

Page 13 of 25 13

## Finishing Touches

Once you have finished all your routing, your board isn’t done quite yet. There are a few last minute checks and finishing touches you should do.
ÿ If you have thin tracks (<25 thou) then it’s nice to add a “chamfer” to any “T”
junctions, thus eliminating any 90 degree angles. This makes the track more
physically robust, and prevents any potential manufacturing etching
problems. But most importantly, it looks nice.
ÿ Check that you have any required mounting holes on the board. Keep mounting holes well clear of any components or tracks. Allow room for any washers and screws.
ÿ Minimise the number of hole sizes. Extra hole sizes cost you money, as the manufacturer will charge you based on not only the number of holes in your boards, but the number of different hole sizes you have. It takes time for the very high speed drill to spin down, change drill bits, and then spin up again. Check with your manufacturer for these costs, but you can’t go wrong by minimising the number of hole sizes.
ÿ Double check for correct hole sizes on all your components. Nothing is more annoying than getting your perfectly laid out board back from the manufacturer, only to find that a component won’t fit in the holes! This is a very common problem, don’t get caught out.
ÿ Ensure that all your vias are identical, with the same pad and hole sizes. Remember your pad to hole ratio. Errors here can cause “breakouts” in your via pad, where the hole, if shifted slightly can be outside of your pad. With plated through holes this is not always fatal, but without a complete annular ring around your hole, your via will be mechanically unreliable.
ÿ Check that there is adequate physical distance between all your components. Watch out for components with exposed metal that can make electrical contact with other components, or exposed tracks and pads.
ÿ Change your display to “draft” mode, which will display all your tracks and pads as outlines. This will allow you to see your board “warts and all”, and will show up any tracks that are tacked on or not ending on pad centers.
ÿ If you wish, add “teardrops” to all your pads and vias. A teardrop is a nice “smoothing out” of
the junction between the track and the pad, not surprisingly, shaped like a teardrop. This
gives a more robust and reliable track to pad interface, better than the almost right angle between a standard track and pad. Don’t add teardrops manually though, it’s a waste of time. But if your program supports automatic teardrop placement, feel free to use it.

## Single Sided Design

Single sided design can greatly reduce the cost of your board. If you can fit your design on a single sided board then it is preferable to do so. Look inside many of today’s consumer items like TV’s and DVD players, and you will almost certainly find some single sided boards. They are still used because they are so cheap to manufacture.
Single sided design however requires some unique techniques which are aren’t required once you go to doubled sided and multi-layer design. It is certainly more challenging than a double sided layout. In fact, a single sided board design will be regarded inversely proportional to the number of jumper links used. No jumper links earns the admiration of many peers!
It is all about a balance between board size and the number of jumper links required. Almost every single sided board will require some jumper links, so it is important to minimise these.
Component placement is even more critical on a single sided board, so this is no time to make all your components nice and neatly aligned. Arrange your components so that they give the shortest and most efficient tracking possible. It is like playing a game Chess, if you don’t think many moves ahead then you will get yourself in a corner pretty quickly. Having just one track running from one side of your board to the other can ruin your whole layout, as it makes routing any other perpendicular tracks impossible.
Many people will route their board as though it is a double sided board, but only with straight tracks on the top layer. Then when the board is to be manufactured, the top layer tracks are replaced with jumper links. This can

Page 14 of 25 14

be a rather inefficient way to approach single sided design, and is not recommended. You must be frugal in your placement, and don’t be afraid to rip everything up and try again if you see a better way to route something. With experience, you will be able to tell before you even start, if a design if worth trying to route on a single sided board.

## Double Sided Design

Double sided design gives an extra degree of freedom for designing your board. Things that were next to impossible on a single sided board become relatively easy when you add an additional layer.
Many (inexperienced) designers tend to become lazy when laying out double sided boards. They think that component placement doesn’t matter all that much, and hundreds of vias can be used to get them out of trouble. They will often lay out components like ICs in neat rows, and then proceed to route everything using a right angle rules. This means that they will route all the tracks on the bottom layer in one direction, and then all the tracks on the top layer perpendicular to the bottom layer. The theory is that if you chop and change between layers enough times you can route almost anything using a “step” type pattern. This technique can be ugly and inefficient, and is a throw back to the old manual tape days. Many basic auto routers work in this way.
Stick to using good component placement techniques and efficient building block routing.
Double sided design can also give you the chance to make use of good ground plane techniques, required for high frequency designs. This will be discussed later.

## Other Layers

There are a few other important layers on your PCB beside the copper track layers.

## Silkscreen

The “silkscreen” layer is also known as the “component overlay” or “component layer”. It is the layer on the top of your board (and bottom if needed) that contains your component outlines, designators (C1, R1 etc), and free text.
This is added to your board using a silkscreening process. White is a standard colour, but other colours are available upon request. You can even mix and match colours on the one board, but that usually costs extra. When designing your board, make sure that you keep all your component designators the same text size, and oriented in the same direction.
When laying out your own component footprints, were possible, make sure that you add a component overlay that reflects the actual size of your component. This way you will be able to tell at a glance how close you can physically position your components. Ensure that all polarised components are marked, and that pin 1 is identified.
Your silkscreen layer will be the most inaccurately aligned of all your layers, so don’t rely on it for any positional accuracy. Ensure that no part of the silkscreen overlaps a bare pad. There is no minimum width requirement for lines on the component overlay, so feel free to use smaller lines and text sizes to fit things in. If parts of the text or lines don’t turn out perfectly on your board then it does not affect your design, unlike tracks and pads.
As a general rule, don’t put component values on the silkscreen, just the component designator.

## Solder Mask

A solder mask is a thin polymer coating on your board which surrounds your pads to help prevent solder from bridging between pins. This is essential for surface mount and fine pitch devices. The solder mask typically covers everything except pads and vias. Your PCB program will automatically remove solder mask from pads and vias. The gap it leaves between the pad and the solder mask is known as the “mask expansion”. The mask expansion should usually be set to at least a few thou. Be careful not to make it too big, or there might be no solder mask between very fine pitch devices.

Page 15 of 25 15

Your solder mask is displayed in your PCB package as a negative image, just like your power plane. Under normal circumstances you don’t need to put anything on your solder mask layer. But if you want to leave the solder mask off a certain part of your board, you can place tracks and fills on your solder mask layer. It is often handy to remove a small square of solder mask from the top of your board, where there are no tracks underneath. This leaves a nice bare and visible part of your board to write something with a pen.
Solder masks come in two types, silkscreen, or “photo imageable”. Photo imageable masks provide better resolution and alignment, and are preferred over silkscreened. You can get different colour solder masks, but the standard colour is green.
On most standard quality boards, the solder mask is laid directly over the bare copper tracks. This is known as Solder Mask Over Bare Copper, or SMOBC. You can get other coatings over your tracks in addition to the solder mask, but these are usually for fairly exotic applications.
You can have vias covered with solder mask if you wish, this is known a tenting. This is useful for close tolerance designs, to prevent solder from flowing into vias.

## Mechanical Layer

The mechanical layer (which may go under other names depending on the package) is used to provide an outline for your board, and other manufacturing instructions. It is not part of your actual PCB design, but is very useful to tell the PCB manufacturer how you want your board assembled. There are no hard and fast rules for this layer, use it however you like, just make sure you tell your PCB manufacturer.

## Keepout

The keepout layer generally defines areas on your board that you don’t want auto or manually routed. This can include clearance areas around mounting hole pads or high voltage components for instance.

## Layer Alignment

When the PCB manufacturer makes your board, there will be alignment tolerances on the artwork film for each layer. This includes track, plane, silkscreen, solder mask, and drilling. If you don’t allow for this in your design, and make your tolerances too fine, you can end up in big trouble. Consult the manufacturer for what alignment tolerances they can achieve, and also what alignment tolerance you are paying for!

## Netlists

A netlist is essentially a list of connections (“nets”) which correspond to your schematic. It also contains the list of components, component designators, component footprints and other information related to your schematic. The netlist file can be generated by your schematic package. Generating a netlist is also called “schematic capture”.
Your PCB package can then import this netlist file and do many things. It can automatically load all the required components onto your blank board. It can also assign a “net” name to each of your component pins. With nets assigned to your PCB components, it is now possible to Auto Route, do Design Rule Checking, and display component connectivity. This is the fundamental concept behind modern Schematic and PCB CAD packages.

Page 16 of 25 16

## Rats Nest


A Typical “Rats Nest” Display. Your job of component placement will be made infinitely easier by having a “rats nest” display enabled. If there is one reason for going to the trouble of drawing up an accurate schematic and importing a netlist, this is surely it. For large designs, a rats nest display is essential.
A rats nest display is one where the program will draw a straight line (not a track) between the pads of components which are connected on the schematic. In effect, it shows the connectivity of your circuit before you start laying out tracks. At the start of your board layout, with all your components placed down randomly, this will appear as a huge and complicated random maze of lines. Hence the name rats nest.
The rats nest may look very daunting at first, but when you move each component the lines will automatically move with them. In this way you can see instantly which components are connected to which, without having to refer back to the schematic and constantly cross reference component designators. Once you have used this feature once, you won’t want to live without it. Even when doing simple designs with a few dozen components, you will miss this functionality.
With the rats nest display enabled, it will be almost possible to lay out all of your components optimally in no time, without having to lay down one single track. The rats nest display will effectively show you what your tracks will connect to. The rats nest lines should disappear when you route your tracks between components, so your design will get less and less “complicated looking” as you go along. When all the rats nest lines disappear, your board is fully routed.

## Design Rule Checking

Design Rule Checking (DRC) allows you to automatically check your PCB design for connectivity, clearance, and other manufacturing errors. With the large and complex PCBs being designed today, it is impractical to manually check a PCB design. This is where the DRC comes into its own, it is an absolutely essential step in professional PCB design.
Examples of what you can check with a DRC are:
ÿ Circuit connectivity. It checks that every track on your board matches the connectivity of your schematic.
ÿ Electrical clearance. You can check the clearance between tracks, pads, and components.


Page 17 of 25 17

ÿ Manufacturing tolerances like min/max hole sizes, track widths, via widths, annulus sizes, and short circuits.
A complete DRC is usually performed after you have finished your PCB. Some packages however have the ability to do “real time” (or “online”) DRC checking as you create your board. For instance, it wont let you connect a track to a pad it shouldn’t go to, or violate a clearance between track and pad. If you have real-time DRC capability, use it, it’s an invaluable tool.

## Forward and Back Annotation

Forward Annotation is when you make changes to your existing PCB layout via the schematic editor. The program will take your schematic netlist and component designators, and import them into your PCB design, and making any relevant changes. Some packages will also automatically remove old PCB tracks that are no longer connected. You can do this at any time during your PCB layout. If you update your schematic, then you must forward annotate into your PCB design. You can do edits like this manually, but forward annotation automates the process.
Back Annotation is when you change one of the component designators (eg. “C1” to “C2”) on your PCB and then automatically update this information back into your Schematic. More advanced back annotation features allow you to swap gates on chips, and perform other electrical changes. There should never be much real need to use back annotation.

## Multi layer Design

Typical 6 Layer PCB Construction

A multi layer PCB is much more expensive and difficult to manufacture than a single or double sided board, but it really does give you a lot of extra density to route power and signal tracks. By having your signals running on the inside of your board, you can pack your components more tightly on your board to give you a more compact design.
Deciding to go from double sided to multi layer can be a big decision, so make sure that a multi layer board is warranted on the grounds of board size and complexity. You can forget about making multi layer boards yourself, it requires a commercial manufacturer. Most of the hobby board suppliers will not do multi layer boards.
Multi layer boards come in even number of layers. With 4, 6, and 8 layer being the most common. You can go many layers above this, but now you are in the realm of the very specialised.
Technically you can get an odd number of layers manufactured, like a 3 layer board for instance. But it really won’t save you any cost over a 4 layer board. In fact a 3 layer board might even be more expensive than a 4 layer board because it calls for a non-standard manufacturing process.
If you decide to go multi layer then make sure you make use all of your layers, there is no point leaving one completely blank.
With a multi layer board, you would typically dedicate one complete layer to a ground plane, and another to your power. With perhaps a few signal tracks thrown on the power layer if you need to. If you have a digital only board, then you’d often dedicate the entire power layer also. If you have room on the top or bottom layer, you can

Page 18 of 25 18

route any additional power rail tracks on there. Power layers are almost always in the middle of the board, with the ground closer to the top layer.
Once you have your power taken care of on the inner layers, you’ll be surprised at the room you now have available for your signal tracks. It really does open up a whole new dimension to routing.
If power planes are vital, and you have a lot of connections to route, then you may have to move from 4 to 6 layers. Six layers will give you four full signal routing layers and two layers dedicated to power. You can really do some advanced routing with 6 layers. Eight layers and above is basically more of the same.
With multi layer design comes the options of using different types of vias to improve your routing density. There are three types of vias - standard, blind, and buried.
Standard vias go through the whole board, and can connect any of the top, bottom or inner layers. These can be wasteful of space on layers which aren’t connected.
“Blind” vias go from the outside surface to one of the inner layers only. The hole does not protrude through the other side of the board. The via is in effect “blind” from the other side of the board.
“Buried” vias only connect two or more inner layers, with no hole being visible on the outside of the board. So the hole is completely buried inside your board.
Blind and buried vias cost more to manufacture than standard vias. But they are very useful, and almost mandatory for very high density designs like those involving Ball Grid Array (BGA) components.

## Power Planes

It is good practice to use “power planes” to distribute power across your board. Using power planes can drastically reduce the power wiring inductance and impedance to your components. This can be vital for high speed digital design for instance. It is good design practice to use power planes whenever possible. They can even be used on double sided boards, if most of your signal tracks are on the top layer.
A power plane is basically one solid copper layer of board dedicated to either your Ground or Power rails, or both. Power planes go in the middle layers of your board, usually on the layers closest to the outer surfaces. On a 4 layer board with complex power requirements it is common to dedicate one layer to your ground plane, and another layer to your various positive and negative power tracks. Your ground rail is usually your signal reference line, so a ground plane is first preference before a power plane is considered.
Many PCB packages have special Power Plane layers that are designed and laid out in reverse to your other normal tracking layers. On a normal tracking layer, your board is assumed to be blank, and you then lay down tracks which will become your actual copper tracks. On a power plane however, your board is assumed to be covered with copper. Laying down tracks on a power plane actually removes the copper. This concept can take some getting used to.
A simple power plane will not have any “tracks” (or removed copper bits) at all on it, but will just be one solid layer of copper. In which case you don’t need to lay down any tracks to remove any copper. However, it is common practice on more complex boards to “split” the power plane by laying down tracks. This may be done to separate an analog and a digital ground, which will reduce the amount of digital ground noise which is coupled into the more sensitive analog circuitry. A typical split power plane would involve a “track” being placed from near your input power connector or main filter capacitors and the opposite edge of the board. Be careful not to accidentally cause a power “loop” on your board by inadvertently connecting the two halves of your plane on the other side of the board.
As a matter of course, you should place “tracks” completely around the outer edge of your board. This will ensure that the power planes do not extend right to the edge of the board. Power planes on the edges of your board can short to not only one another, but also to any guide rails or mounting hardware.
You don’t have to use the actual Power Plane layer on your PCB package if you don’t want to. You can use a regular signal layer and lay down copper fills and tracks yourself. Power Planes layers though often have some advantages that will vary from one PCB package another.

Page 19 of 25 19

## Good Grounding

Grounding is fundamental to the operation of many circuits. Good or bad grounding techniques can make or break your design. There are several grounding techniques which are always good practices to incorporate into any design.
ÿ Use copper, and lots of it. The more copper you have in your ground path, the lower the impedance. This is highly desirable for many electrical reasons. Use polygon fills and planes where possible.
ÿ Always dedicate one of your planes to ground on multi-layer boards. Make it the layer closest to the top layer.
ÿ Run separate ground paths for critical parts of your circuit, back to the main filter capacitor(s). This is known as “star” grounding, because the ground tracks all run out from a central point, often looking like a star. In fact, try and do this as matter of course, even if your components aren’t critical. Separate ground lines keep current and noise from one component from affecting other components.
ÿ If using a ground plane, utilise “split” plane techniques to give effective star grounding.
ÿ “stitch” required points straight through to your ground plane, don’t use any more track length than you need.
ÿ Use multiple vias to decrease your trace impedance to ground.

## Good Bypassing

Active components and points in your circuit which draw significant switching current should always be “bypassed”. This is to “smooth” out your power rail going to a particular device. “Bypassing” is using a capacitor across your power rails as physically and electrically close to the desired component or point in your circuit as possible. A typical bypass capacitor value is 100nF, although other values such as 1uF, 10nF and 1nF are often used to bypass different frequencies. You can even have two or three different value capacitors in parallel.
When bypassing, you CANNOT replace multiple capacitors with one single capacitor, it defeats the entire purpose of bypassing! It is not uncommon for a large design to have hundreds of bypass capacitors.
As a general rule, you should use at least one bypass capacitor per IC or other switching component if possible. Common values of bypass capacitors are 100nF for general purpose use, 10nF or 1nF for higher frequencies, and 1uF or 10uF for low frequencies.
Special low Equivalent Series Resistance (ESR) capacitors are sometimes used on critical designs such as switch mode power supplies.
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

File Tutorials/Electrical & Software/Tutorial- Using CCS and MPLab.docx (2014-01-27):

PIC Tutorial

1. Download/install MPLab IDE 8.8 from http://www.microchip.com/stellent/idcplg?IdcService=SS_GET_PAGE&nodeId=1406&dDocName=en019469

2. Copy over the CCS folder from the solarcar server

- in your file explorer, type this into the address bar: \\pc-solarcar.eng.mcmaster.ca

- user: remote , pass: phoenix

- CCS is in: files->software->CCS PCWHD

3. Installing CCS

- run pcwhdupd.exe

- it will ask for registration files. Don’t give any registration files and complete the installation

- run the keygen (in the CCS folder) and place files in the main part of the PIC C folder (C: -> program files (x86) -> PICC, unless you put it somewhere else). The keygen produces the registration files and keeping them in the PICC folder will enable them.

- run ideutilsupd.exe (in CCS folder)

- download and install the MPLab plug-in for CCS found here: http://www.ccsinfo.com/downloads.php

- to check if everything worked correctly: run the PIC C compiler ->project ->PIC Wizard. If you cannot select the PIC Wizard button, OR if there are no Devices to choose from while in the PIC Wizard, follow the next step. If you have these options, you are good.

- go to the Solarcar server -> files -> software ->CCS PCWHD ->example crg. Copy the registration files from there and replace your old files in your PICC folder with them. Everything should work now.

4. Starting a new project

- open PIC C and run the PIC Wizard. Save the project file somewhere

- in the setup menu, choose the correct device (we used PIC 16F883), correct frequency (we used 8,000,000), if you are not using an external oscillator: select internal RC Osc, go into Intr Oscillator Config-> and enable internal Oscillator.

- what this does is write a lot of the setup code and functions for you

- open MPLab and run the Project Wizard.

- select the same device as you did before

-under active toolsuite, select CCS C Compiler. If your computer did not find it for you, hit browse then: C->program (x86)->PICC->Ccsc.exe

- name and save the new project somewhere

- in step 4, find the CCS .c file that you created and ADD it to the right column.

- now the .c file is linked between the compiler and MPLab

5. Begin coding!

-PICC has a really good help search to look for functions

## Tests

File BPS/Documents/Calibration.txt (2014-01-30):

Hall effect sensor calibration:
Sensor measurement range:
Sensor output range: 

formula experimentally determined:
read_adc() = 680.24 * current + 32685

Voltage sensor calibration:
Sensor measurement range:  0.00V .. 4.75V
Sensor output range: 0 .. 1024

Divide value from sensor by 1024 to normalize the range to 0.0 to 1.0, then multiply by 5.0? to get the maximum voltage range from the sensor.

Temperature Sensor Calibration:
Sensor measurement range: -127°C .. 127°C
Sensor output range: -1024 .. 1024

Divide value from sensor by 1024 to normalize the range to -1.0 to 1.0, then multiply by 127? to get the maximum temperature range from the sensor. This is effectively the same as dividing by 8 or shifting 3 bits to the right, or, more simply, removing the 3 least significant bits.

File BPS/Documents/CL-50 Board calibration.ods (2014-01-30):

current | read_adc()
0.09 | 32750
0.65 | 33130
1.08 | 33421
1.33 | 33592
1.40 | 33634
1.82 | 33918
2.12 | 34128
2.28 | 34234
2.48 | 34365
2.84 | 34615
3.36 | 34972
3.82 | 35280
4.26 | 35592
 |  | Trendline Equation:
 |  | read_adc() = 680.244 * current + 32685

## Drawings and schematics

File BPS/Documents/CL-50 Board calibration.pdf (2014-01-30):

## CL-50 Board Calibration

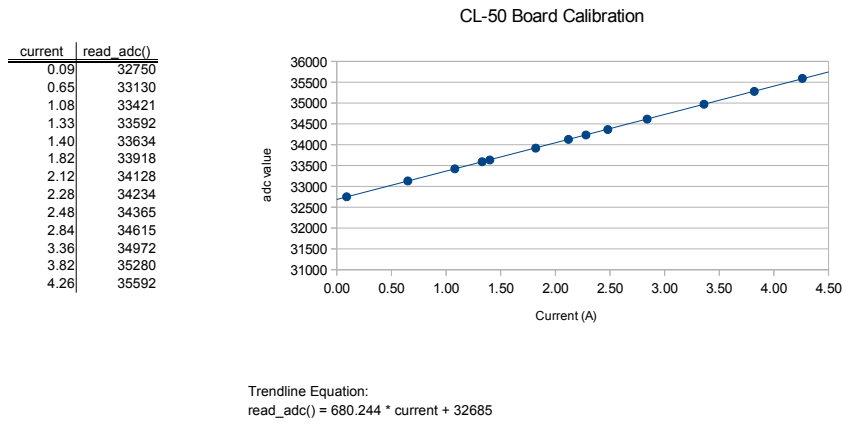
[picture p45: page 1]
current; read_adc(); Trendline Equation: read_adc() = 680.244 * current + 32685; Current (A); adc value

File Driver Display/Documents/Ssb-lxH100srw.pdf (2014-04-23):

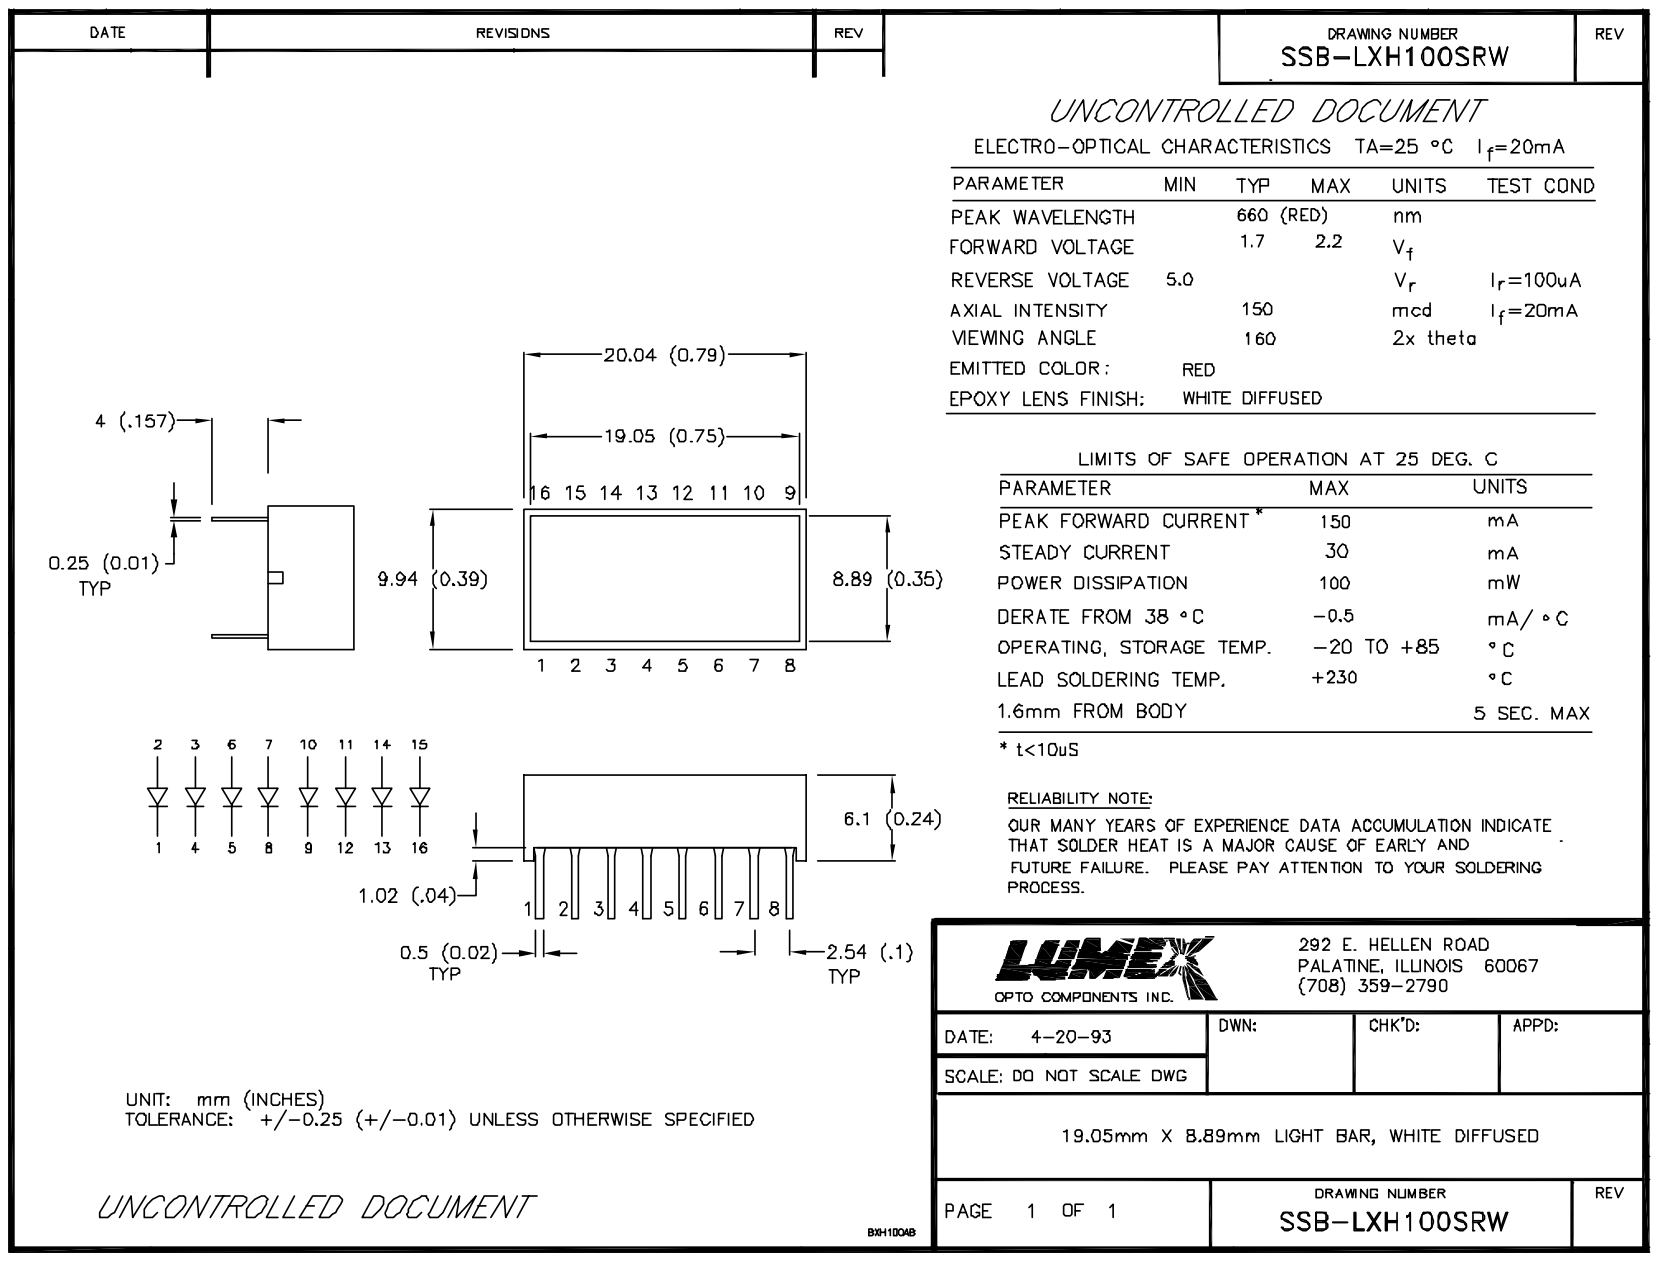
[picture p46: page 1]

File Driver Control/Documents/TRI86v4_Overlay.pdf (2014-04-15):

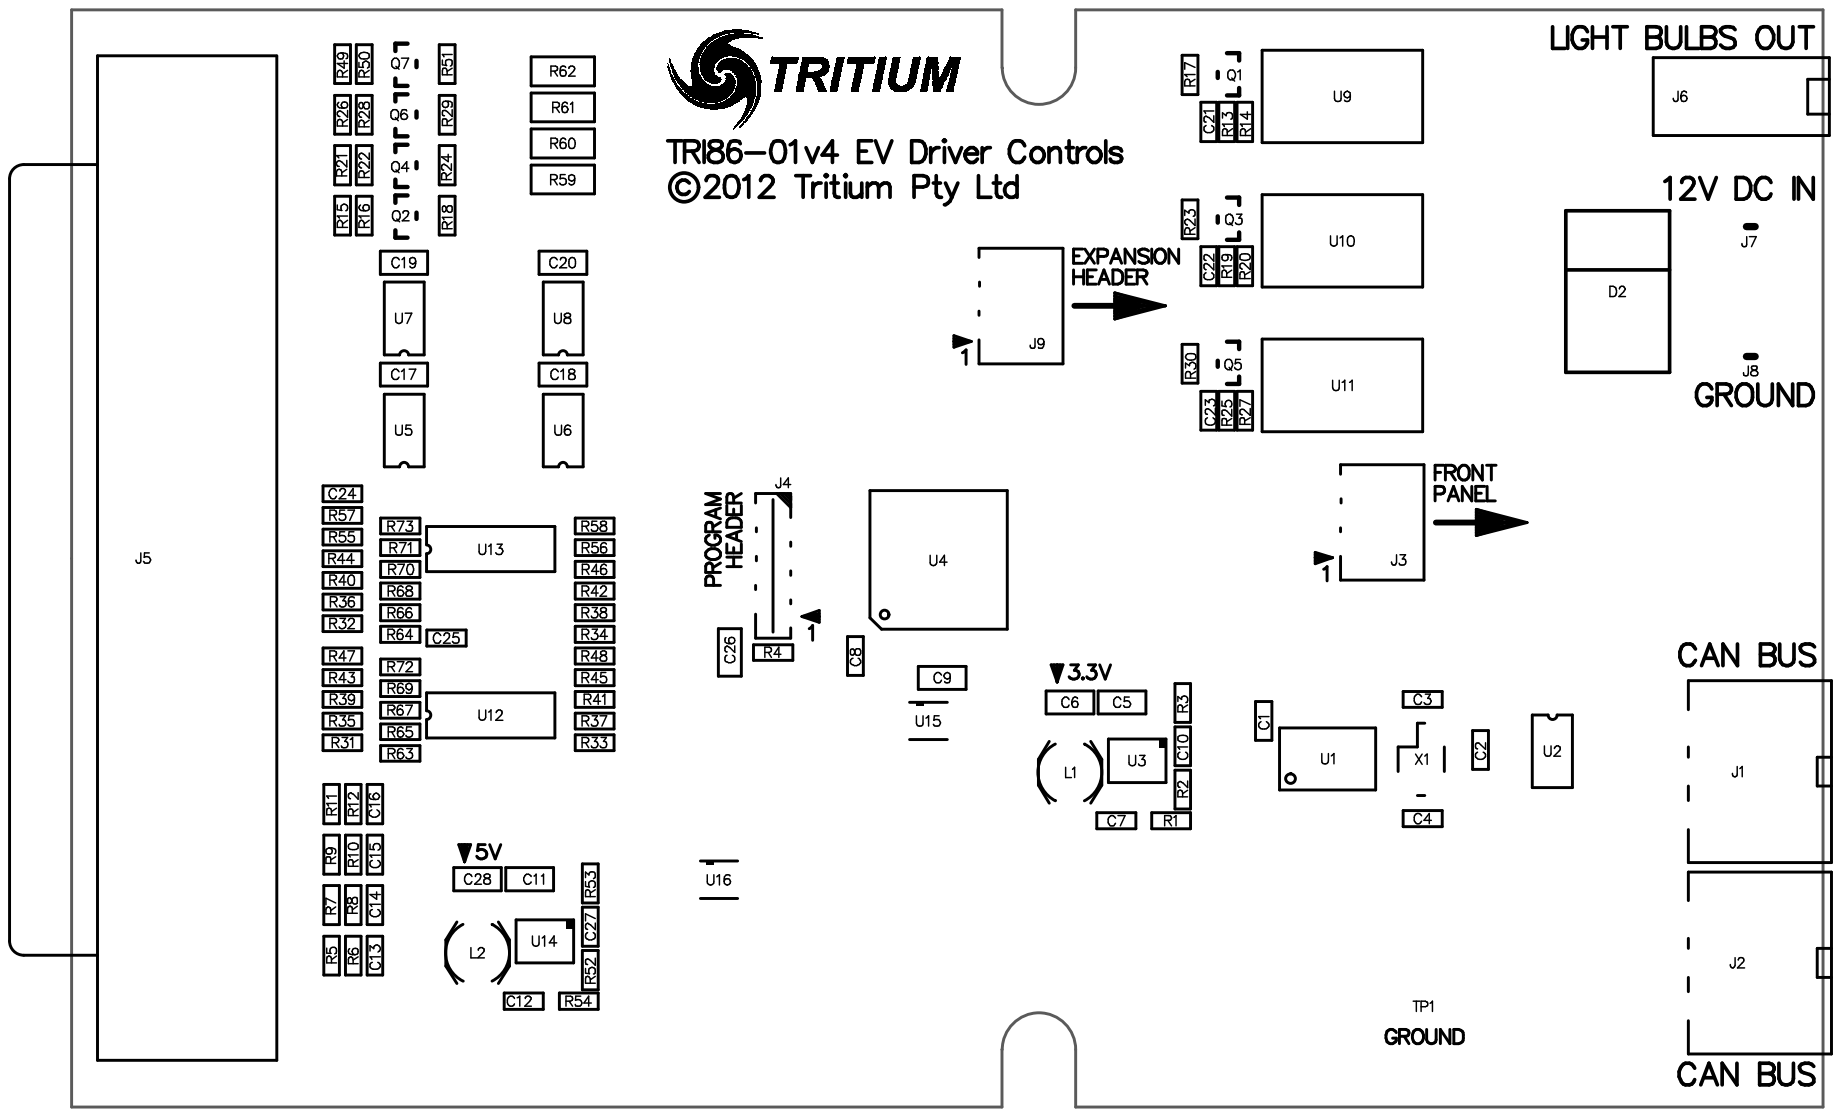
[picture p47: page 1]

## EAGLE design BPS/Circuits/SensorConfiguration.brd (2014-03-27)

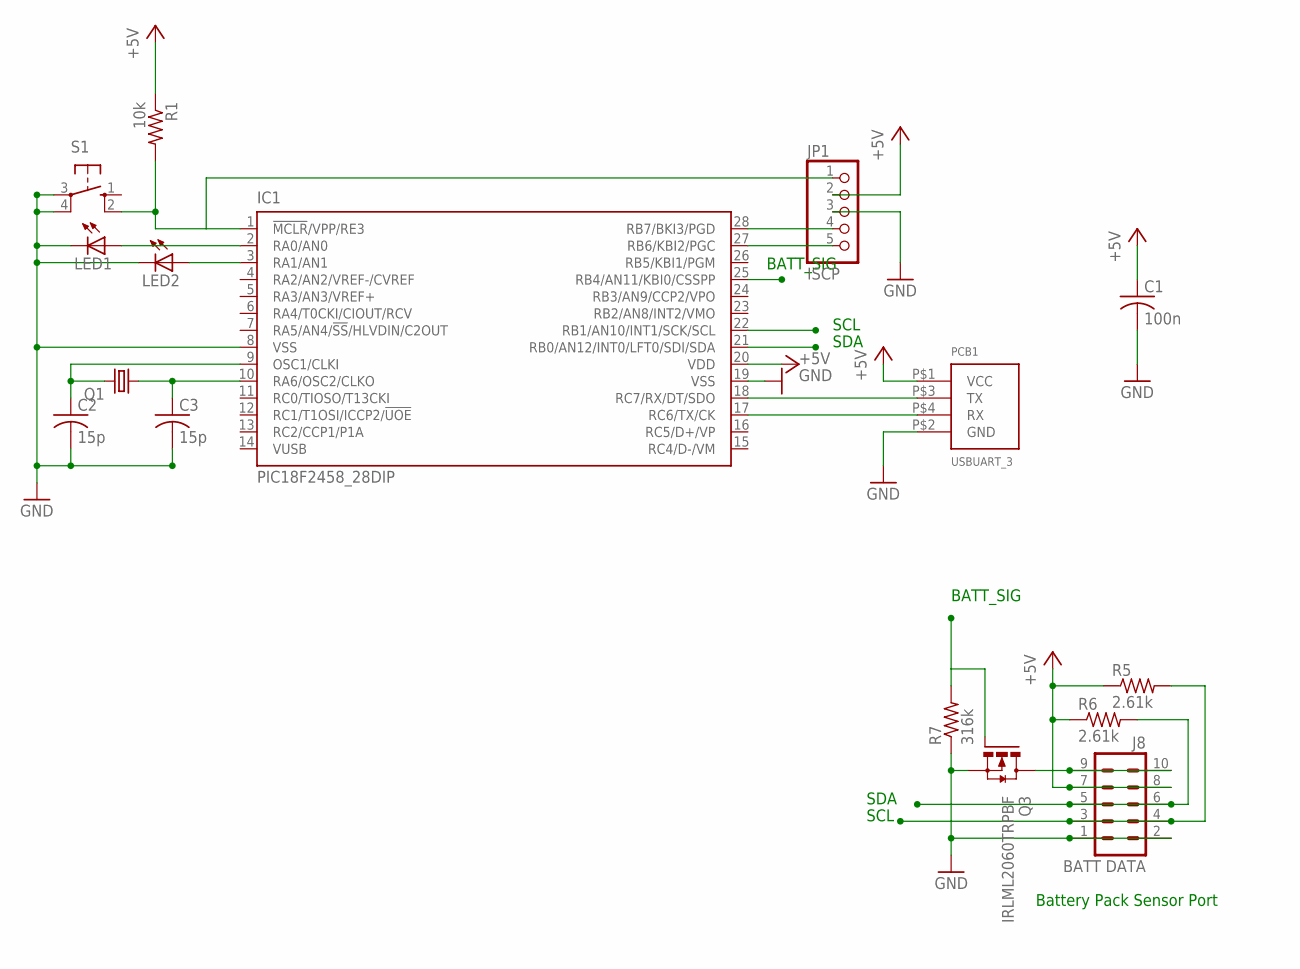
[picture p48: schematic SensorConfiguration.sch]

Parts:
C1: 100n; C0805
C2, C3: 15p; C0805
IC1: PIC18F2458_28DIP; DIL28-3
J8: BATT DATA; ML10
JP1: ISCP; 1X05
LED1, LED2: LED5MM
PCB1: USBUART_3; UB232R
Q1: CRYSTALHC49S; HC49/S
Q3: IRLML2060TRPBF; SOT23
R1: 10k; R0805
R5, R6: 2.61k; R0805
R7: 316k; R0805
S1: 10-XX; B3F-10XX

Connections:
+5V: C1.1, IC1.20 (VDD), J8.7, J8.8, JP1.2, PCB1.P$1 (VCC), R1.1, R5.1, R6.1
BSIG: IC1.25 (RB4/AN11/KBI0/CSSPP), Q3.1 (G), R7.2
GND: C1.2, C2.2, C3.2, IC1.8 (VSS), IC1.19 (VSS), J8.1, J8.2, JP1.3, LED1.K (C), LED2.K (C), PCB1.P$2 (GND), Q3.2 (S), R7.1, S1.3, S1.4 (P1)
unnamed: IC1.27 (RB6/KBI2/PGC), JP1.5
unnamed: IC1.18 (RC7/RX/DT/SDO), PCB1.P$3 (TX)
unnamed: IC1.17 (RC6/TX/CK), PCB1.P$4 (RX)
unnamed: IC1.28 (RB7/BKI3/PGD), JP1.4
unnamed: IC1.1 (!MCLR!/VPP/RE3), JP1.1, R1.2, S1.2 (S1)
unnamed: IC1.2 (RA0/AN0), LED1.A
unnamed: J8.9, J8.10, Q3.3 (D)
unnamed: IC1.3 (RA1/AN1), LED2.A
unnamed: C2.1, IC1.9 (OSC1/CLKI), Q1.2
unnamed: C3.1, IC1.10 (RA6/OSC2/CLKO), Q1.1
SCL: IC1.22 (RB1/AN10/INT1/SCK/SCL), J8.3, J8.4, R5.2
SDA: IC1.21 (RB0/AN12/INT0/LFT0/SDI/SDA), J8.5, J8.6, R6.2

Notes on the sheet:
SCL
SDA
Battery Pack Sensor Port
BATT_SIG

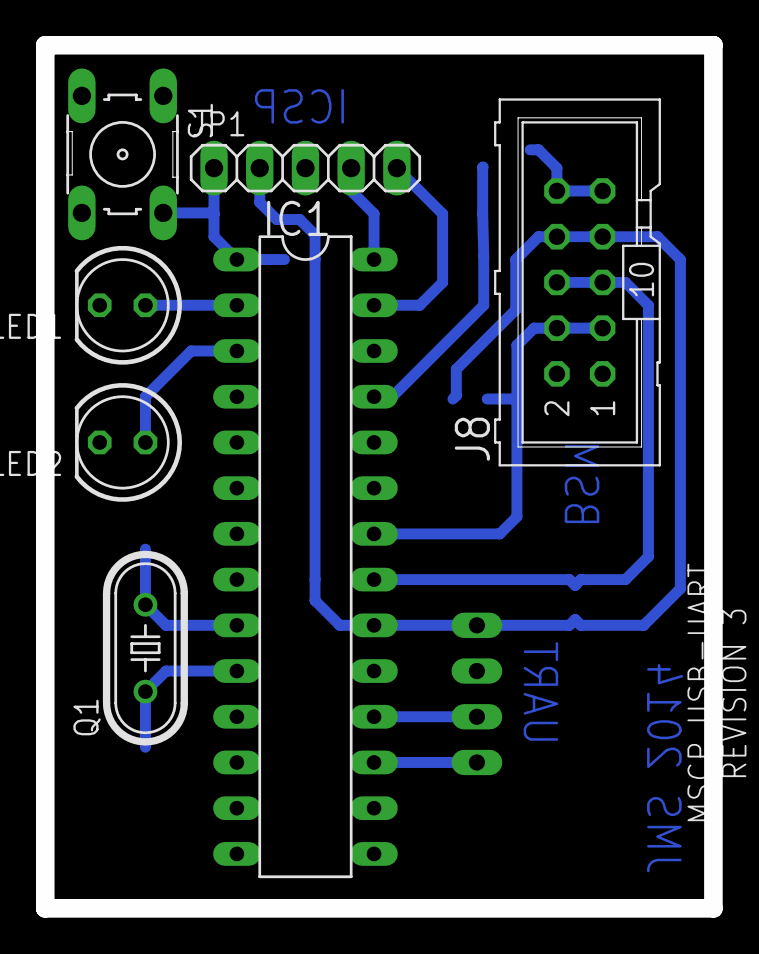
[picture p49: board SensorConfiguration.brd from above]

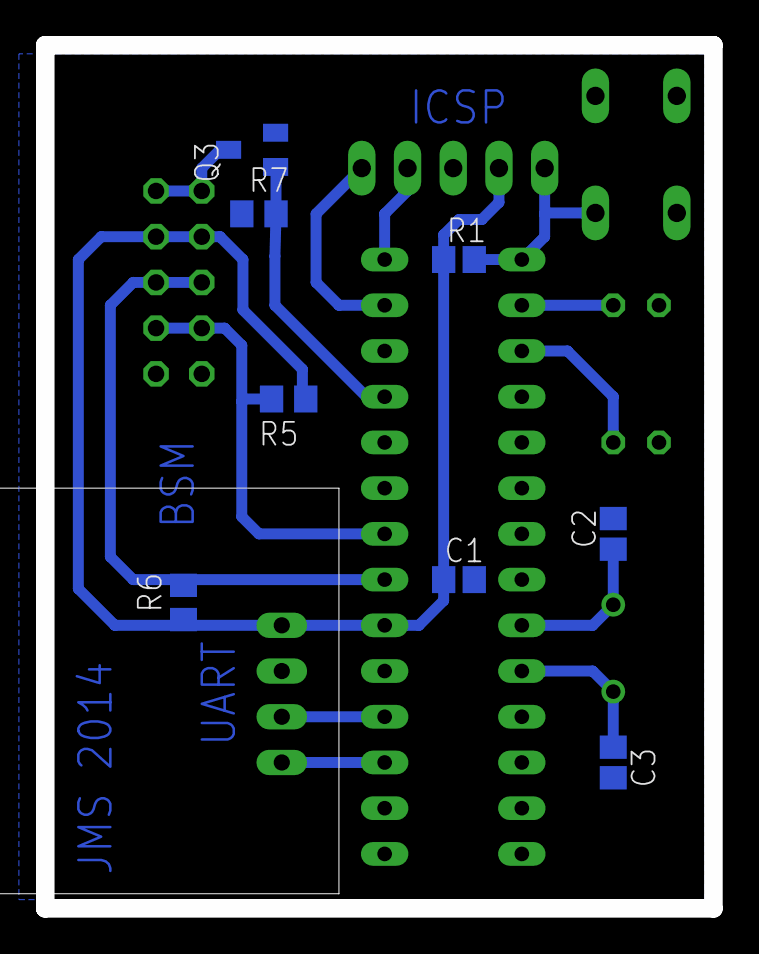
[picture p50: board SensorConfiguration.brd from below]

Board: 2 copper layers, 37.1 x 48.0 mm, 16 parts (8 on the bottom side), 15 nets.

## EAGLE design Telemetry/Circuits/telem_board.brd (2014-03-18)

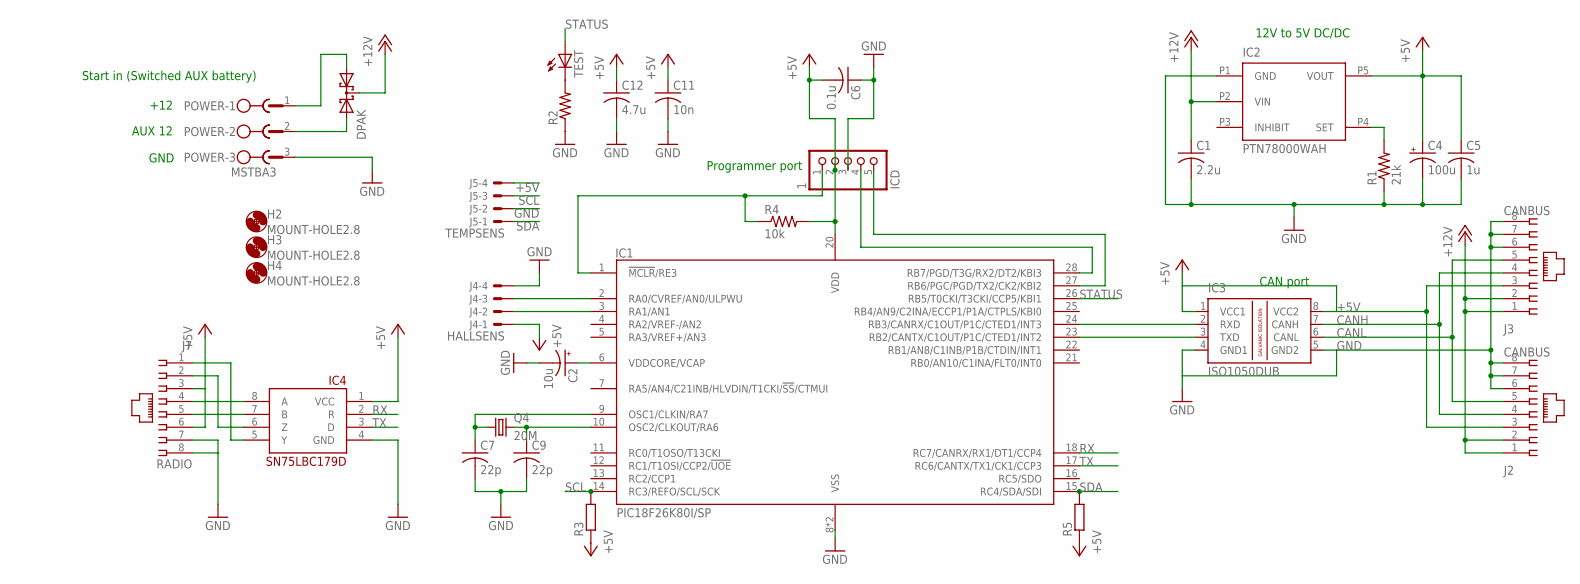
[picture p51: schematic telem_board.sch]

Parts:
1: ICD; 1X05
C1: 2.2u; C1206
C2: 10u; TT2D4
C4: 100u; SMC_D
C5: 1u; C0805
C6: 0.1u; C0805
C7, C9: 22p; C0805
C11: 10n; C0805
C12: 4.7u; C0805
DPAK: DIODE_2SCHOTTKY-DPAK; DPAK
H2, H3, H4: MOUNT-HOLE2.8; 2,8
IC1: PIC18F26K80I/SP; DIL28/3
IC2: PTN78000WAH; PTN78000
IC3: ISO1050DUB; DUB-R-PDSO-G8
IC4: SN75LBC179D; SO08
J2, J3: CANBUS; 215877-7
J4: HALLSENS; 6410-04
J5: TEMPSENS; 6410-04
J7: RADIO; 215877-7
POWER: MSTBA3
Q4: 20M; HC49/S
R1: 21k; R0805
R2: R-US_R0805; R0805
R3, R5: R; R0805
R4: 10k; R0805
TEST: LEDCHIP-LED0805; CHIP-LED0805

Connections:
+5V: 1.2, C4.+, C5.1, C6.2, C11.1, C12.1, IC1.20 (VDD), IC2.P5 (VOUT), IC3.1 (VCC1), IC3.8 (VCC2), IC4.1 (VCC), J2.3, J3.3, J4.1, J5.4, J7.3, J7.6, R3.1, R4.2, R5.1
+12V: C1.1, DPAK.3 (C), IC2.P2 (VIN), J2.1, J2.2, J3.1, J3.2
CANH: IC3.7 (CANH), J2.4, J3.4
CANL: IC3.6 (CANL), J2.5, J3.5
GND: 1.3, C1.2, C2.-, C4.-, C5.2, C6.1, C7.2, C9.2, C11.2, C12.2, IC1.8 (VSS), IC1.19 (VSS), IC2.P1 (GND), IC3.4 (GND1), IC3.5 (GND2), IC4.4 (GND), J2.6, J2.7, J2.8, J3.6, J3.7, J3.8, J4.4, J5.2, J7.7, J7.8, POWER.3, R1.1, R2.1
unnamed: IC1.2 (RA0/CVREF/AN0/ULPWU), J4.3
unnamed: IC1.3 (RA1/AN1), J4.2
unnamed: IC4.7 (B), J7.5
unnamed: IC4.8 (A), J7.4
unnamed: C2.+, IC1.6 (VDDCORE/VCAP)
unnamed: IC1.23 (RB2/CANTX/C1OUT/P1C/CTED1/INT2), IC3.3 (TXD)
unnamed: R2.2, TEST.C
unnamed: IC2.P4 (SET), R1.2
unnamed: IC1.24 (RB3/CANRX/C1OUT/P1C/CTED1/INT3), IC3.2 (RXD)
unnamed: IC4.6 (Z), J7.2
unnamed: IC4.5 (Y), J7.1
unnamed: DPAK.1 (A1), POWER.1
unnamed: DPAK.2 (A2), POWER.2
unnamed: 1.4, IC1.28 (RB7/PGD/T3G/RX2/DT2/KBI3)
unnamed: 1.5, IC1.27 (RB6/PGC/PGD/TX2/CK2/KBI2)
unnamed: 1.1, IC1.1 (!MCLR!/RE3), R4.1
unnamed: C7.1, IC1.9 (OSC1/CLKIN/RA7), Q4.1
unnamed: C9.1, IC1.10 (OSC2/CLKOUT/RA6), Q4.2
RX: IC1.18 (RC7/CANRX/RX1/DT1/CCP4), IC4.2 (R)
SCL: IC1.14 (RC3/REFO/SCL/SCK), J5.3, R3.2
SDA: IC1.15 (RC4/SDA/SDI), J5.1, R5.2
STATUS: IC1.26 (RB5/T0CKI/T3CKI/CCP5/KBI1), TEST.A
TX: IC1.17 (RC6/CANTX/TX1/CK1/CCP3), IC4.3 (D)

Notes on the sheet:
12V to 5V DC/DC
Programmer port
CAN port
Start in (Switched AUX battery)
+12
GND
AUX 12

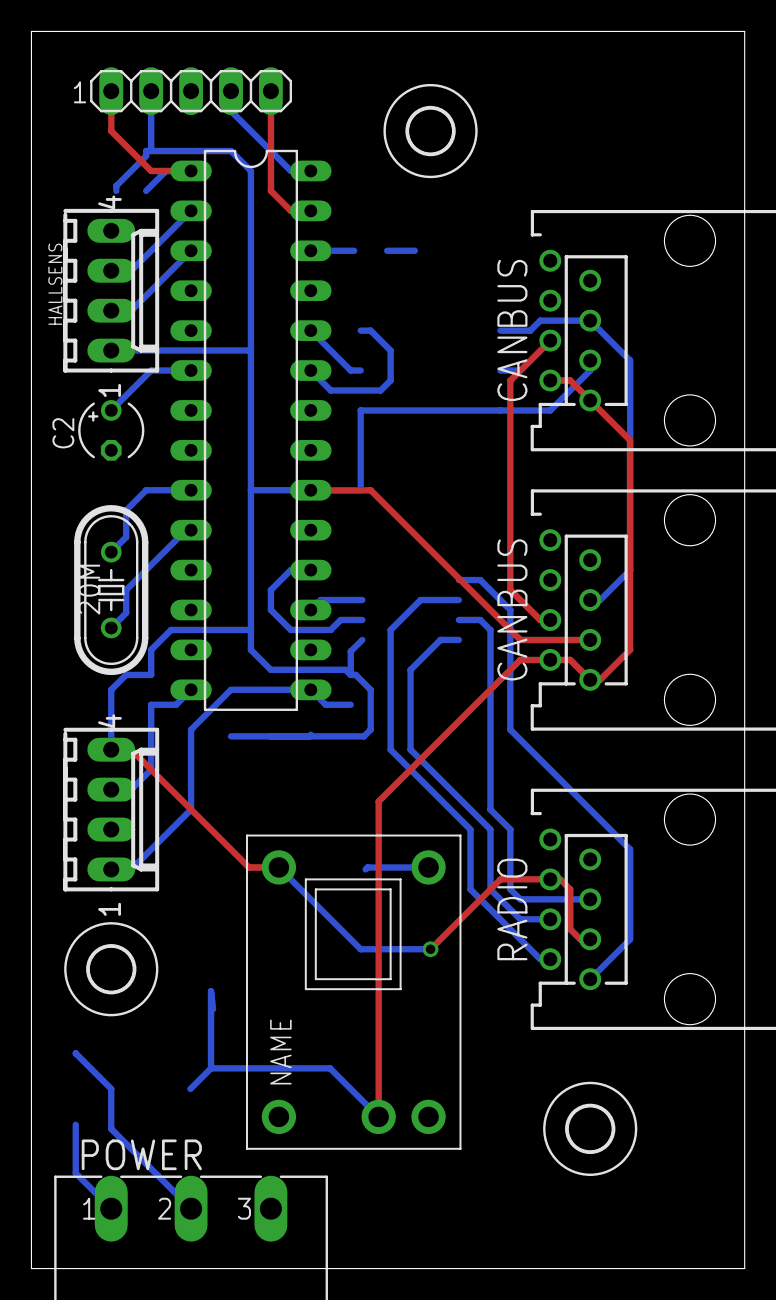
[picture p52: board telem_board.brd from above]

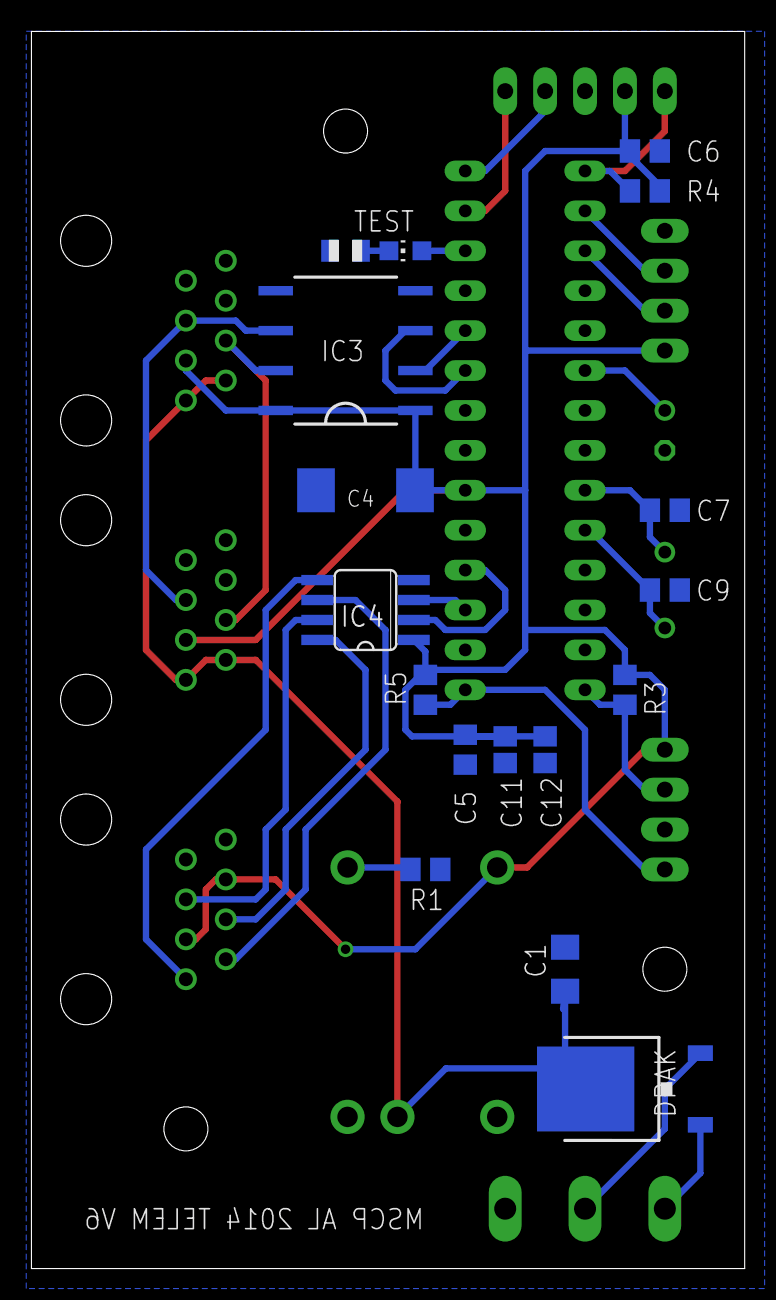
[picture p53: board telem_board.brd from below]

Board: 2 copper layers, 45.4 x 78.7 mm, 31 parts (17 on the bottom side), 28 nets.

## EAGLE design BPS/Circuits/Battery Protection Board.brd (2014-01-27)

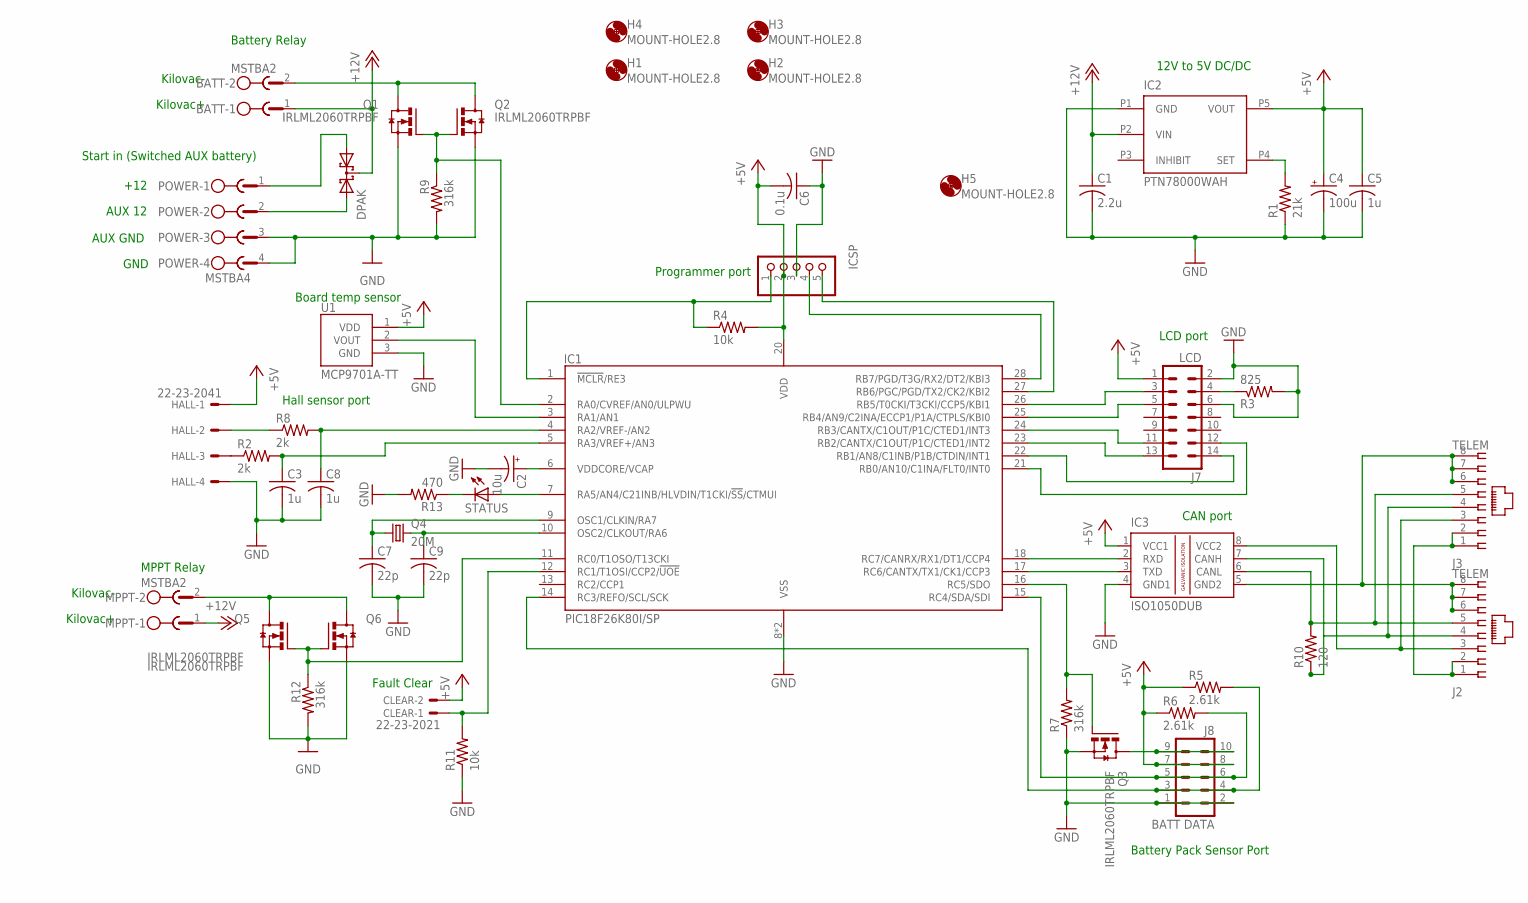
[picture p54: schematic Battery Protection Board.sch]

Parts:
BATT: MSTBA2
C1: 2.2u; C1206
C2: 10u; TT2D4
C3, C5, C8: 1u; C0805
C4: 100u; SMC_D
C6: 0.1u; C0805
C7, C9: 22p; C0805
CLEAR: 22-23-2021
DPAK: DIODE_2SCHOTTKY-DPAK; DPAK
H1, H2, H3, H4, H5: MOUNT-HOLE2.8; 2,8
HALL: 22-23-2041
IC1: PIC18F26K80I/SP; DIL28/3
IC2: PTN78000WAH; PTN78000
IC3: ISO1050DUB; DUB-R-PDSO-G8
ICSP: ICD; 1X05
J2, J3: TELEM; 215877-7
J7: LCD; ML14
J8: BATT DATA; ML10
MPPT: MSTBA2
POWER: MSTBA4
Q1, Q2, Q3, Q5, Q6: IRLML2060TRPBF; SOT23
Q4: 20M; HC49/S
R1: 21k; R0805
R2, R8: 2k; R0805
R3: 825; R0805
R4, R11: 10k; R0805
R5, R6: 2.61k; R0805
R7, R9, R12: 316k; R0805
R10: 120; 0207/7
R13: 470; R0805
STATUS: LED5MM
U1: MCP9701A-TT; SOT23

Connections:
+5V: C4.+, C5.1, C6.2, CLEAR.2, HALL.1, IC1.20 (VDD), IC2.P5 (VOUT), IC3.1 (VCC1), ICSP.2, J7.1, J8.7, J8.8, R4.2, R5.1, R6.1, U1.1 (VDD)
+12V: BATT.1, C1.1, DPAK.3 (C), IC2.P2 (VIN), MPPT.1
GND: C1.2, C2.-, C3.2, C4.-, C5.2, C6.1, C7.2, C8.2, C9.2, HALL.4, IC1.8 (VSS), IC1.19 (VSS), IC2.P1 (GND), IC3.4 (GND1), ICSP.3, J7.2, J7.6, J8.1, J8.2, POWER.3, POWER.4, Q1.2 (S), Q2.2 (S), Q3.2 (S), Q5.2 (S), Q6.2 (S), R1.1, R3.2, R7.1, R9.2, R11.1, R12.2, R13.2, U1.3 (GND)
unnamed: IC1.27 (RB6/PGC/PGD/TX2/CK2/KBI2), ICSP.5
unnamed: J7.4, R3.1
unnamed: IC1.15 (RC4/SDA/SDI), J8.5, J8.6, R6.2
unnamed: IC1.16 (RC5/SDO), Q3.1 (G), R7.2
unnamed: C2.+, IC1.6 (VDDCORE/VCAP)
unnamed: IC1.3 (RA1/AN1), U1.2 (VOUT)
unnamed: J8.9, J8.10, Q3.3 (D)
unnamed: IC2.P4 (SET), R1.2
unnamed: IC1.7 (RA5/AN4/C21INB/HLVDIN/T1CKI/!SS!/CTMUI), STATUS.A
unnamed: IC1.14 (RC3/REFO/SCL/SCK), J8.3, J8.4, R5.2
unnamed: IC1.17 (RC6/CANTX/TX1/CK1/CCP3), IC3.3 (TXD)
unnamed: DPAK.2 (A2), POWER.2
unnamed: DPAK.1 (A1), POWER.1
unnamed: IC3.7 (CANH), J2.4, J3.4, R10.1
unnamed: IC3.8 (VCC2), J2.3, J3.3
unnamed: J2.1, J2.2, J3.1, J3.2
unnamed: IC1.22 (RB1/AN8/C1INB/P1B/CTDIN/INT1), J7.14
unnamed: IC1.18 (RC7/CANRX/RX1/DT1/CCP4), IC3.2 (RXD)
unnamed: IC1.21 (RB0/AN10/C1INA/FLT0/INT0), J7.12
unnamed: IC1.1 (!MCLR!/RE3), ICSP.1, R4.1
unnamed: IC1.28 (RB7/PGD/T3G/RX2/DT2/KBI3), ICSP.4
unnamed: IC1.23 (RB2/CANTX/C1OUT/P1C/CTED1/INT2), J7.13
unnamed: IC1.24 (RB3/CANTX/C1OUT/P1C/CTED1/INT3), J7.11
unnamed: C7.1, IC1.9 (OSC1/CLKIN/RA7), Q4.1
unnamed: C9.1, IC1.10 (OSC2/CLKOUT/RA6), Q4.2
unnamed: IC1.25 (RB4/AN9/C2INA/ECCP1/P1A/CTPLS/KBI0), J7.5
unnamed: C8.1, IC1.4 (RA2/VREF-/AN2), R8.2
unnamed: IC1.26 (RB5/T0CKI/T3CKI/CCP5/KBI1), J7.3
unnamed: IC1.2 (RA0/CVREF/AN0/ULPWU), Q1.1 (G), Q2.1 (G), R9.1
unnamed: R13.1, STATUS.K (C)
unnamed: C3.1, IC1.5 (RA3/VREF+/AN3), R2.2
unnamed: IC3.5 (GND2), J2.6, J2.7, J2.8, J3.6, J3.7, J3.8
unnamed: HALL.3, R2.1
unnamed: IC1.11 (RC0/T1OSO/T13CKI), Q5.1 (G), Q6.1 (G), R12.1
unnamed: HALL.2, R8.1
unnamed: BATT.2, Q1.3 (D), Q2.3 (D)
unnamed: MPPT.2, Q5.3 (D), Q6.3 (D)
unnamed: CLEAR.1, IC1.12 (RC1/T1OSI/CCP2/!UOE!), R11.2
unnamed: IC3.6 (CANL), J2.5, J3.5, R10.2

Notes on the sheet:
Start in (Switched AUX battery)
+12
Kilovac+
Kilovac-
LCD port
12V to 5V DC/DC
Programmer port
CAN port
Board temp sensor
Hall sensor port
Battery Relay
MPPT Relay
Fault Clear
GND
AUX 12
AUX GND
Battery Pack Sensor Port

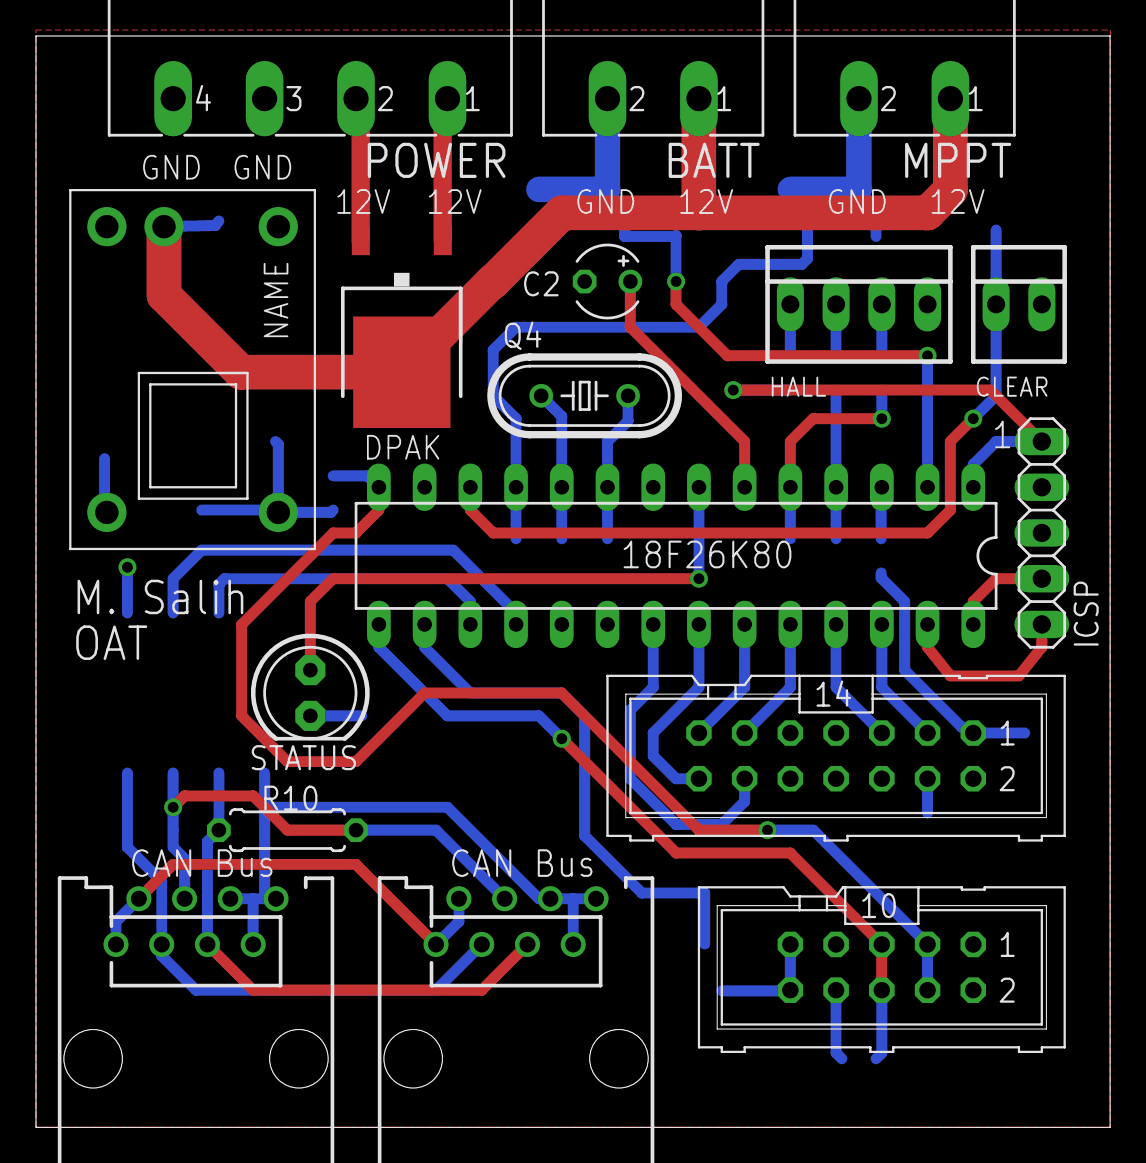
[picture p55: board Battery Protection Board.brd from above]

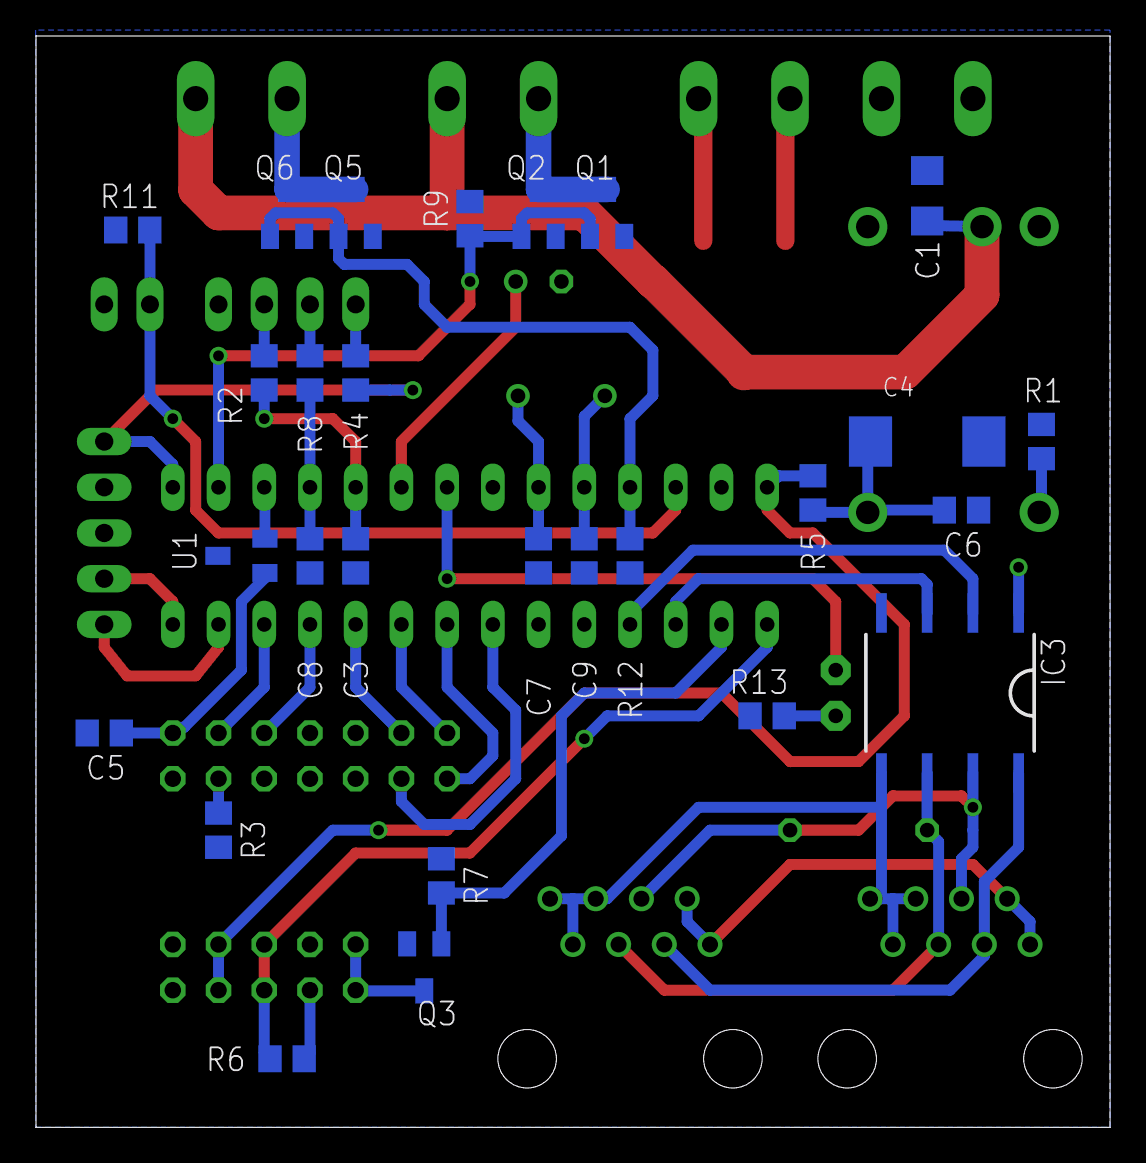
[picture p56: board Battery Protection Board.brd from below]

Board: 2 copper layers, 59.7 x 60.6 mm, 49 parts (27 on the bottom side), 42 nets.

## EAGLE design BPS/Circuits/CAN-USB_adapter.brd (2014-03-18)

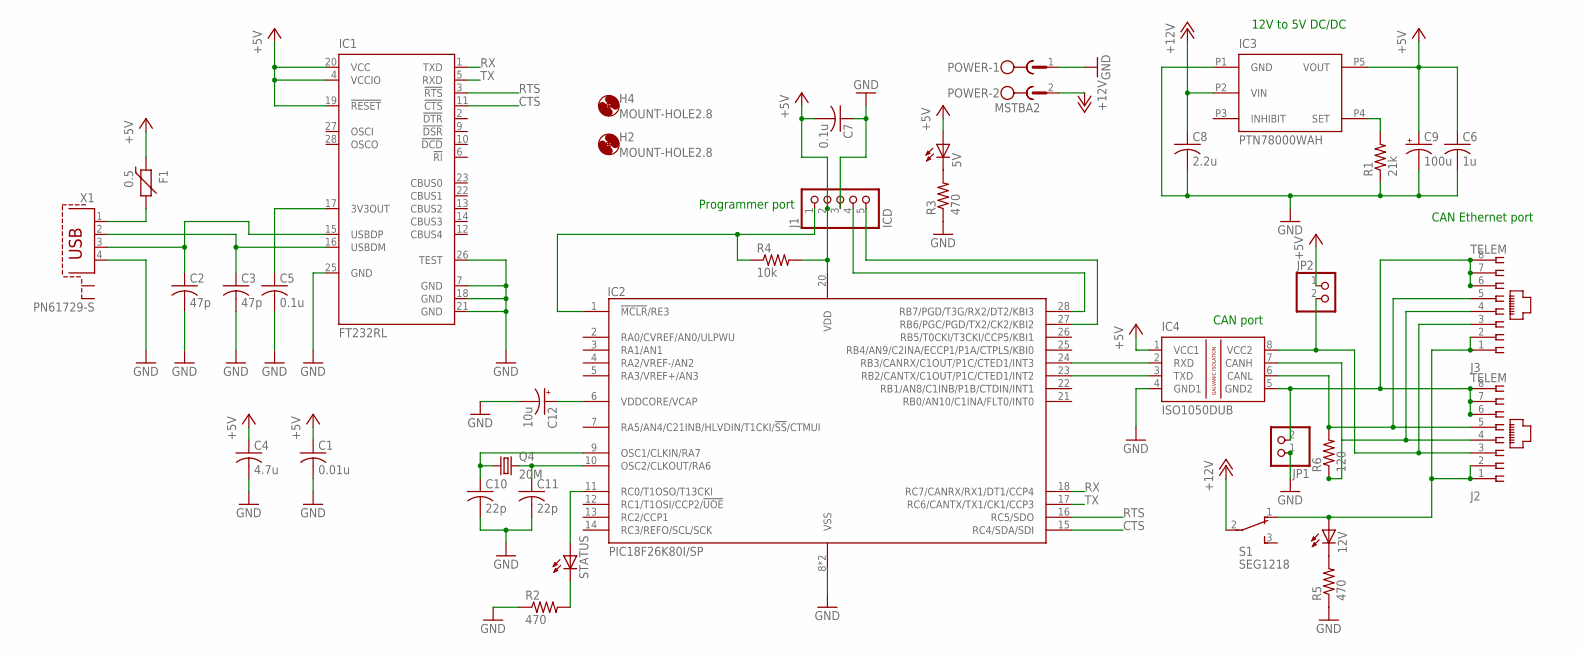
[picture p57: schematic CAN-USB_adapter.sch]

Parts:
5V, 12V: LED5MM
C1: 0.01u; C0805
C2, C3: 47p; C0805
C4: 4.7u; C0805
C5, C7: 0.1u; C0805
C6: 1u; C0805
C8: 2.2u; C1206
C9: 100u; SMC_D
C10, C11: 22p; C0805
C12: 10u; TT2D4
F1: 0.5; F1206
H2, H4: MOUNT-HOLE2.8; 2,8
IC1: FT232RL; SSOP28
IC2: PIC18F26K80I/SP; DIL28/3
IC3: PTN78000WAH; PTN78000
IC4: ISO1050DUB; DUB-R-PDSO-G8
J1: ICD; 1X05
J2, J3: TELEM; 215877-7
JP1, JP2: PINHD-1X2; 1X02
POWER: MSTBA2
Q4: 20M; HC49/S
R1: 21k; R0805
R2, R3, R5: 470; R0805
R4: 10k; R0805
R6: 120; 0207/7
S1: SEG1218; EG1218
STATUS: LED5MM
X1: PN61729-S

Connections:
+5V: 5V.A, C1.1, C4.1, C6.1, C7.2, C9.+, F1.1, IC1.4 (VCCIO), IC1.19 (!RESET), IC1.20 (VCC), IC2.20 (VDD), IC3.P5 (VOUT), IC4.1 (VCC1), J1.2, JP2.1, R4.2
+12V: C8.1, IC3.P2 (VIN), POWER.2, S1.2
CTS: IC1.11 (!CTS), IC2.15 (RC4/SDA/SDI)
GND: C1.2, C2.2, C3.2, C4.2, C5.2, C6.2, C7.1, C8.2, C9.-, C10.2, C11.2, C12.-, IC1.7 (GND), IC1.18 (GND), IC1.21 (GND), IC1.25 (GND), IC1.26 (TEST), IC2.8 (VSS), IC2.19 (VSS), IC3.P1 (GND), IC4.4 (GND1), J1.3, JP1.1, POWER.1, R1.1, R2.1, R3.1, R5.1, X1.4
unnamed: C3.1, IC1.16 (USBDM), X1.2
unnamed: C2.1, IC1.15 (USBDP), X1.3
unnamed: C5.1, IC1.17 (3V3OUT)
unnamed: IC2.28 (RB7/PGD/T3G/RX2/DT2/KBI3), J1.4
unnamed: IC2.27 (RB6/PGC/PGD/TX2/CK2/KBI2), J1.5
unnamed: IC2.24 (RB3/CANRX/C1OUT/P1C/CTED1/INT3), IC4.2 (RXD)
unnamed: F1.2, X1.1
unnamed: IC3.P4 (SET), R1.2
unnamed: IC2.23 (RB2/CANTX/C1OUT/P1C/CTED1/INT2), IC4.3 (TXD)
unnamed: R2.2, STATUS.K (C)
unnamed: C10.1, IC2.9 (OSC1/CLKIN/RA7), Q4.1
unnamed: C11.1, IC2.10 (OSC2/CLKOUT/RA6), Q4.2
unnamed: IC2.11 (RC0/T1OSO/T13CKI), STATUS.A
unnamed: C12.+, IC2.6 (VDDCORE/VCAP)
unnamed: 5V.K (C), R3.2
unnamed: 12V.A, J2.1, J2.2, J3.1, J3.2, S1.1 (O)
unnamed: 12V.K (C), R5.2
unnamed: IC4.8 (VCC2), J2.3, J3.3, JP2.2
unnamed: IC2.1 (!MCLR!/RE3), J1.1, R4.1
unnamed: IC4.5 (GND2), J2.6, J2.7, J2.8, J3.6, J3.7, J3.8, JP1.2
unnamed: IC4.7 (CANH), J2.4, J3.4, R6.1
unnamed: IC4.6 (CANL), J2.5, J3.5, R6.2
RTS: IC1.3 (!RTS), IC2.16 (RC5/SDO)
RX: IC1.1 (TXD), IC2.18 (RC7/CANRX/RX1/DT1/CCP4)
TX: IC1.5 (RXD), IC2.17 (RC6/CANTX/TX1/CK1/CCP3)

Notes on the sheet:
12V to 5V DC/DC
Programmer port
CAN port
CAN Ethernet port

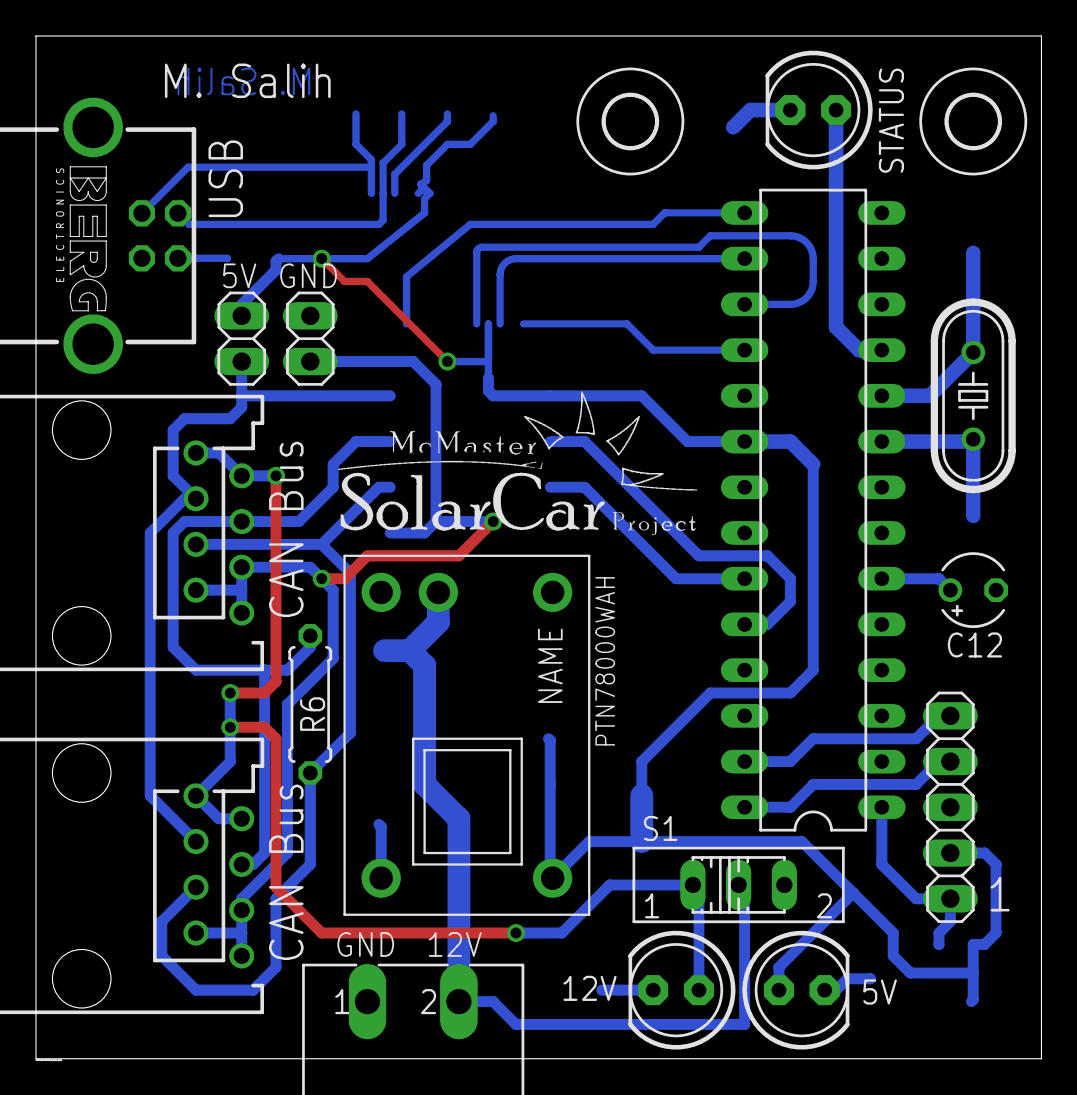
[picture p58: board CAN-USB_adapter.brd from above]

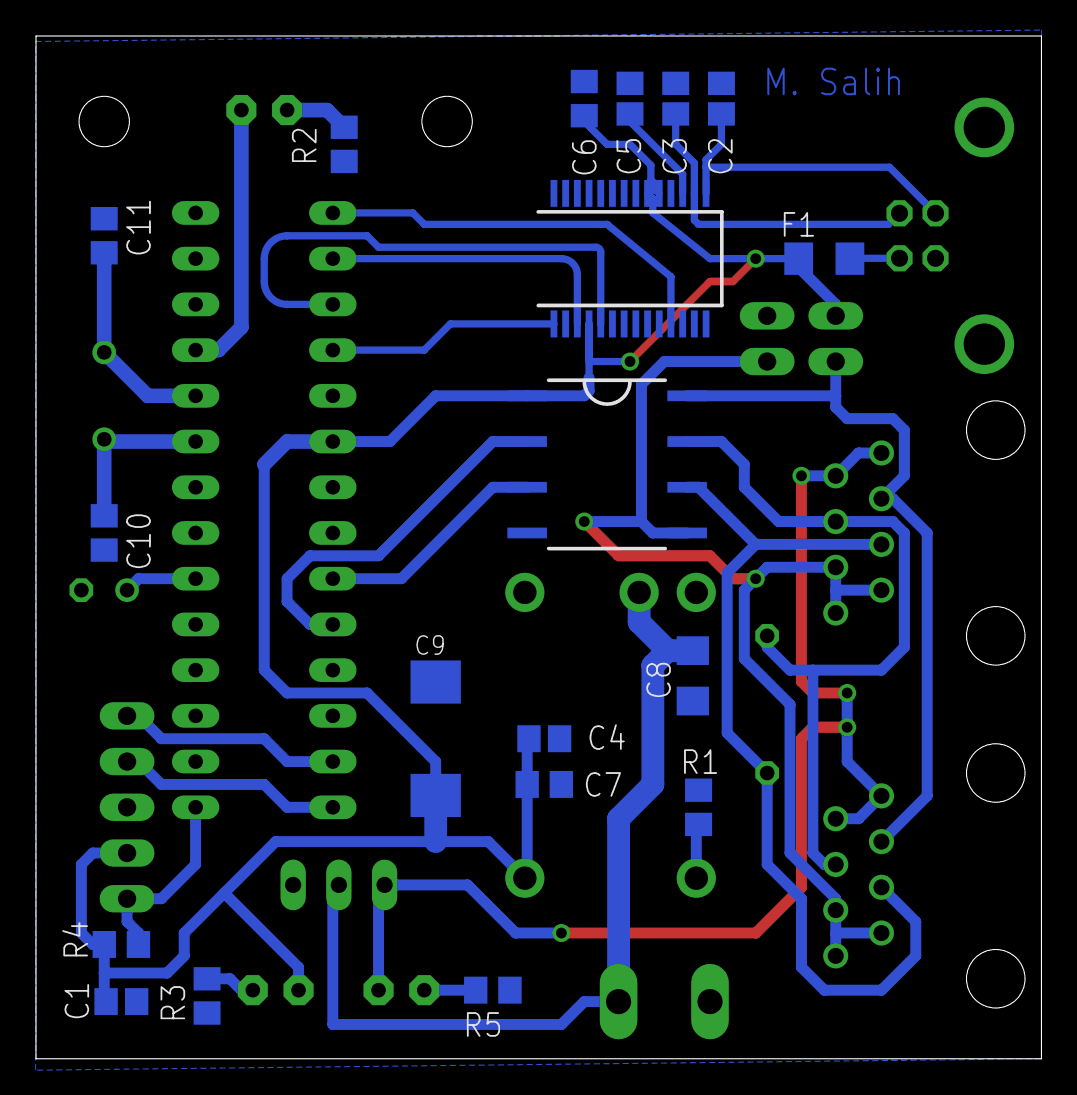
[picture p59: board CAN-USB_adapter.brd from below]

Board: 2 copper layers, 55.9 x 56.8 mm, 37 parts (19 on the bottom side), 29 nets.

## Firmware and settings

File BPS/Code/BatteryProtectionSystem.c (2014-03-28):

/* McMaster University Solar Car Club
 * Fireball II January 20 2014
 * Battery Protection Team
 *
 * Paul Correia
 * Lun Li
 * -------------------------
 * Version History:
 *
 * 03/24/2014 - Uncalibrated Beta
 */

#include <18F26K80.h>   //Library for PIC used (18F26K80)
#device adc = 16

#FUSES NOWDT            // No Watch Dog Timer
#FUSES HSH              // High speed Osc, high power 16MHz-25MHz
#FUSES NOPLLEN          // 4X HW PLL disabled, 4x PLL enabled in software

#FUSES SOSC_DIG         // Digital mode, I/O port functionality of RC0 and RC1
#FUSES NOXINST          // Extended set extension and Indexed Addressing mode disabled(Legacy mode)
#FUSES BROWNOUT         // Reset when brownout detected
#FUSES PUT              // Power Up Timer
#FUSES NOIESO           // Internal External Switch Over mode disabled
#FUSES NOFCMEN          // Fail-safe clock monitor disabled
#FUSES NOPROTECT        // Code not protected from reading
#FUSES CANC             // CANTX and CANRX pins are located on RC6 and RC7

// Preprocessor Macros
// uC pins
#define LED             PIN_A5
#define BATT_RELAY      PIN_A0
#define MPPT_RELAY      PIN_C0
#define SENSOR_RELAY    PIN_C5
#define I2C_SDA_PIN     PIN_C4
#define I2C_SCL_PIN     PIN_C3

#define I2C_WRITE_BIT 0
#define I2C_READ_BIT 1
#define ADC_CHANNEL 1

// Voltage and temperature sensor registers (check sensor DATASHEET for more info
#define VOLT_REGISTER   0x0C
#define TEMP_REGISTER   0x18

// Threshold values for voltage, temperature and current
// To convert voltage values, divide by 5.0V and multiply by 1023
// To convert temperature values, divide by 127 degC and multiply by 1023
#define VOLT_MAX_WARN   818     // 4.0V
#define VOLT_MAX_ERROR  860     // 4.2V
#define VOLT_MIN_WARN   717     // 3.0V
#define VOLT_MIN_ERROR  573     // 2.8V
#define TEMP_CHARGE_MAX_WARN        225 // degC
#define TEMP_CHARGE_MAX_ERROR       240 // degC
#define TEMP_DISCHARGE_MAX_WARN     225 // 28degC
#define TEMP_DISCHARGE_MAX_ERROR    240 // 30degC
#define CURRENT_CHARGE_MAX_WARN         0 //to be announced
#define CURRENT_CHARGE_MAX_ERROR        0
#define CURRENT_DISCHARGE_MAX_WARN      0
#define CURRENT_DISCHARGE_MAX_ERROR     0

// Error and warning codes
#define NONE            0x00
#define VOLT_HIGH       0x01
#define VOLT_LOW        0x02
#define TEMP_HIGH       0x04
#define TEMP_LOW        0x08
#define CURRENT_HIGH    0x10
#define CURRENT_LOW     0x20
#define WARN_BIT        0x40
#define ERROR_BIT       0x80

// Code checking
#define IS_VOLT_CODE(x)     ((x) & (VOLT_HIGH | VOLT_LOW))
#define IS_TEMP_CODE(x)     ((x) & (TEMP_HIGH | TEMP_LOW))
#define IS_CURRENT_CODE(x)  ((x) & (CURRENT_HIGH | CURRENT_LOW))
#define IS_WARNING(x)       ((x) & WARN_BIT)
#define IS_ERROR(x)         ((x) & ERROR_BIT)

// Typedefs
typedef unsigned int8 uint8;
typedef unsigned int16 uint16;

typedef struct SensorData {
    uint8 ID;
    uint16 voltData, tempData;
    int1 overVoltFlag, underVoltFlag, overTempFlag;
    uint8 overVoltCount, underVoltCount;
    uint8 overTempCount;
};

typedef struct HallEffectData {
    uint16 data;
    uint8 overCount;
    int1 overFlag;
};

#use delay(clock = 20000000)
#use i2c(master, sda = I2C_SDA_PIN, scl = I2C_SCL_PIN)
#include <../../Shared/Code/can-18F4580_mscp.c>  //CAN library
#include <../../Shared/Code/flex_lcd_library.c>  //LCD library

const uint16 updateInterval = 1000; // ms
const uint8 maxErrorCount = 4;
const uint8 numSensors = 14;
struct SensorData sensor[numSensors];
struct HallEffectData hallSensor;
uint16 rawCurrentData = 0xABCD;

// Keep track of sensor with greatest/least voltage and temperature, and their
// corresponding sensor readings, so we can print them to the LCD
uint16 minVolt, maxVolt, maxTemp;
uint8 minVoltNum, maxVoltNum, maxTempNum;

uint16 ms = 0;
int8 packetNum = 0;

const int32 tx_id = 0x800;  // To be changed later
const int tx_pri = 3;
const int1 tx_rtr = 0;
const int1 tx_ext = 0;

// Function prototypes
void setup(void);
void initSensors(void);
uint8 updateSensor(uint8 n);

void LCD_Send(void);
int CANBus_SendData(void);
int setPacketData(int8 packet, uint8* data);

uint8 getErrCode(uint16 voltReading, uint16 tempReading);
uint8 getHallErrorCode(uint16 hallReading);
int1 hallDischarge(void);

uint16 getRawSensorVal(uint8 sensorNum, uint8 sensorRegister);
uint16 getRawCurrentVal(void);
uint16 combineBytes(uint8 high, uint8 low);

// Interrupt service routines
#int_timer2
void isr_timer2(void) {
    ms++;
}

// Use length of can frame to tell wether or not its an error message
// 8 bytes is normal data flow, less is error message
// Over/Under Volt/Temp - Send error code, sensor, and reading. (3 Bytes)
// Over/Under current - Send error code and reading. (2 Bytes)

//setup
void setup(void) {
    output_high(LED);
    output_high(BATT_RELAY);
    output_high(MPPT_RELAY);
    
    setup_comparator(NC_NC_NC_NC);
    setup_adc(ADC_CLOCK_DIV_32);
    setup_adc_ports(ALL_ANALOG);
    set_adc_channel(ADC_CHANNEL);
    
    setup_timer_2(T2_DIV_BY_4,79,16);
    enable_interrupts(INT_TIMER2);
    enable_interrupts(GLOBAL);
    
    can_init();    //initialize CANBus
    lcd_init();    //initialize LCD
    initSensors();  //set sensor IDs and default values
    
    set_tris_c((*0xF94 & 0xBF) | 0x80); // Set C7 to input, C6 to output
    
    // Close relay on each sensor to physically enable it
    output_high(SENSOR_RELAY);
}

/*
 *  initSensors
 *
 *  Initializes the sensorIDs, sets the error counts and data values to 0 for
 *  every temperature/voltage sensor, as well as the hall effect sensor.
 */
void initSensors(void) {
    int i;

    // Initialize volt/temp sensors
    sensor[0].ID = 0x05;
    sensor[1].ID = 0x15;
    sensor[2].ID = 0x0;
    sensor[3].ID = 0x0;
    sensor[4].ID = 0x0;
    sensor[5].ID = 0x0;
    sensor[6].ID = 0x0;
    sensor[7].ID = 0x0;
    sensor[8].ID = 0x0;
    sensor[9].ID = 0x0;
    sensor[10].ID = 0x0;
    sensor[11].ID = 0x0;
    sensor[12].ID = 0x0;
    sensor[13].ID = 0x0;

    for (i=0; i<numSensors; i++) {
        sensor[i].tempData = 0;
        sensor[i].voltData = 0;
        sensor[i].overTempCount = 0;
        sensor[i].overVoltCount = 0;
        sensor[i].underVoltCount = 0;
    }
    
    // Initialize current sensor
    hallSensor.data = 0xABCD;
    hallSensor.overCount = 0;
}

void main(void) {
    
    setup();
    
    uint8 i;
    uint8 warnFlag = 0;
    uint8 errCode;
    
    output_low(LED);
    
    while(1) {
        if (ms <= updateInterval)
            continue;
        // else
        ms = 0;
        output_low(LED);
        
        // Reset min and max volt/temp
        minVolt=0xFFFF;
        maxVolt=0;
        maxTemp=0;
        
        for(i = 0; i < numSensors; i++) {
            errCode = updateSensor(i);
            
            if (sensor[i].voltData > maxVolt) {
                maxVolt = sensor[i].voltData;
                maxVoltNum = i;
            }
            if (sensor[i].voltData < minVolt) {
                minVolt = sensor[i].voltData;
                minVoltNum = i;
            }
            if (sensor[i].tempData > maxTemp) {
                maxTemp = sensor[i].tempData;
                maxTempNum = i;
            }
            
            // If the sensor is in the normal operating range, move on to the
            // next one
            if (errCode == NONE)
                continue;
            
            if (IS_ERROR(errCode)) {
                // Check if any of the counters have gone over the max count
                if (sensor[i].overVoltCount >= maxErrorCount ||
                    sensor[i].underVoltCount >= maxErrorCount ||
                    sensor[i].overTempCount >= maxErrorCount) {
                    // If ANY of the sensors have an error, turn off the relays
                    // They can never be turned back on until the program is
                    // reset.
                    output_low(BATT_RELAY);
                    output_low(MPPT_RELAY);  
                    output_high(LED); 
                }
            }
        }
        
        rawCurrentData = getRawCurrentVal();
                
        LCD_Send();
        CANBus_SendData();
    }
}

/*
 *  updateSensor
 *
 *  Reads the specified sensor's voltage and temperature values, compares these
 *  readings to their corresponding threshold values. If any readings are above
 *  their ERROR threshold, their error counter is incremented.
 *
 *  Arguments:
 *  n - Sensor number
 *  
 *  Return:
 *  Error and/or warning code
 */
uint8 updateSensor(uint8 n) {
    uint8 err = NONE;
    
    sensor[n].voltData = getRawSensorVal(sensor[n].ID, VOLT_REGISTER);
    sensor[n].tempData = getRawSensorVal(sensor[n].ID, TEMP_REGISTER);
    sensor[n].overVoltFlag = 0;
    sensor[n].underVoltFlag = 0;
    sensor[n].overTempFlag = 0;
    
    err = getErrCode(sensor[n].voltData, sensor[n].tempData);
    
    // The behaviour when an error bit isn't set may be changed to decrement the
    // counter instead of reseting it.
       
    if (err & VOLT_HIGH) {
        sensor[n].overVoltFlag = 1;
    
        if (IS_ERROR(err))
            sensor[n].overVoltCount++;
        else 
            sensor[n].overVoltCount--;
    }
    
    if (err & VOLT_LOW) {
        sensor[n].underVoltFlag = 1;
    
        if (IS_ERROR(err))
            sensor[n].underVoltCount++;
        else 
            sensor[n].underVoltCount--;
    }
    
    if (err & TEMP_HIGH) {
        sensor[n].overTempFlag = 1;
    
        if (IS_ERROR(err))
            sensor[n].overTempCount++;
        else 
            sensor[n].overTempCount--;
    }
    
    return err;
}

float rawToVolt(int16 rawVolt) {
    return (float)rawVolt * 0.0048876;
}
float rawToTemp(int16 rawTemp) {
    return (float)rawTemp/0.12414;
}
float rawToCurr(int16 rawCurr) {
    return ((float)rawCurr - 32685.0) * 0.0014701;
}

// Send data to LCD
void LCD_Send(void) {
    char buffer[32];
    
    sprintf(buffer, "V:%4.2f #%02d, v:%4.2f #%2d", 
                    rawToVolt(maxVolt), maxVoltNum, 
                    rawToVolt(minVolt), minVoltNum);
    lcd_gotoxy(0,0);
    printf(lcd_putc, buffer);
    sprintf(buffer, "T:%4.1f #%02d, curr=%5.2f", 
                    rawToTemp(maxTemp), maxTempNum, 
                    rawToCurr(hallSensor.data));
    lcd_gotoxy(0,1);
    printf(lcd_putc, buffer);
}

/*
 *  CANBus_SendData
 *
 *  Sends normal sensor data along the CAN bus. Data is set in setPacketData()
 *  and is sent in this function. Also increments the packet number
 *
 *  Return:
 *  response from can_putd, 0xFF if write failed, otherwise returns buffer that
 *  can_putd wrote to
 *
 */
int CANBus_SendData(void) {
    int8 response;
    int tx_len;
    
    // does this even need to be initd to 0s? yes
    uint8 out_data[8] = {0,0,0,0,0,0,0,0};
    
    tx_len = setPacketData(packetNum, out_data);
    response = can_putd(tx_id+packetNum,out_data,tx_len,tx_pri,tx_ext,tx_rtr);
    
    // Check if the data was written successfully
    if(response != 0xFF) {
        //output_toggle(LED);    
        packetNum = 2;
        //packetNum = (packetNum + 1) % 5;
    }
    
    return(response);
}

int setPacketData(int8 packetNum, uint8* data) {
    uint16 i;
    int packetLength = 8;
    
    switch(packetNum) { 
    case 0:
        for(i = 0; i < 8; i++)
            data[i] = (uint8)(sensor[i].voltData>>2);
        break;
    case 1:
        for(i = 0; i < 6; i++)
            data[i] = (uint8)(sensor[i+8].voltData>>2);
        data[7] = (uint8)(rawCurrentData>>8);
        data[8] = (uint8)rawCurrentData;
        break;
    case 2:
        for(i = 0; i < 8; i++)
            data[i] = (uint8)(sensor[i].tempData>>2);
        break;
    case 3:
        packetLength = 6;
        for(i = 0; i < 6; i++)
            data[i] = (uint8)(sensor[i+8].tempData>>2);
        break;
    case 4:
        packetLength = 6;        
        // Sensor 0 to 7
        for (i = 0; i < 8; i++) {
            data[0] |= sensor[i].overVoltFlag << (7 - i);
            data[2] |= sensor[i].underVoltFlag << (7 - i);
            data[4] |= sensor[i].overTempFlag << (7 - i);
        }        
        // Sensor 8 to 13
        for (i = 0; i < 6; i++) {
            data[1] |= sensor[i+8].overVoltFlag << (7 - i);
            data[3] |= sensor[i+8].underVoltFlag << (7 - i);
            data[5] |= sensor[i+8].overTempFlag << (7 - i);
        }        
        data[5] |= hallSensor.overFlag;
        break;
    }
    return(packetLength);
}

uint8 getErrCode(uint16 voltReading, uint16 tempReading) {
    uint8 ret = NONE;
    uint16 tempWarnThresh, tempErrThresh;
    
    if (voltReading >= VOLT_MAX_WARN) {
        ret |= VOLT_HIGH | WARN_BIT;
        
        if (voltReading >= VOLT_MAX_ERROR)
            ret |= ERROR_BIT;
    } else if (voltReading <= VOLT_MIN_WARN){
        ret |= VOLT_LOW | WARN_BIT;
        
        if (voltReading <= VOLT_MIN_ERROR)
            ret |= ERROR_BIT;
    }
        
    if (hallDischarge()) {
        tempWarnThresh = TEMP_DISCHARGE_MAX_WARN;
        tempErrThresh = TEMP_DISCHARGE_MAX_ERROR;
    } else {
        tempWarnThresh = TEMP_CHARGE_MAX_WARN;
        tempErrThresh = TEMP_CHARGE_MAX_ERROR;
    }
        
    if (tempReading >= tempWarnThresh) {
        ret |= TEMP_HIGH | WARN_BIT;
        
        if (tempReading >= tempErrThresh)
            ret |= ERROR_BIT;
    }
    
    return ret;
}

uint8 getHallErrorCode(uint16 hallReading) {

    uint8 ret = NONE;
    uint16 warnThresh, errThresh;
    
    // get appropriate threshold for charge/discharge
    if (hallDischarge()) {
        warnThresh = CURRENT_DISCHARGE_MAX_WARN;
        errThresh = CURRENT_DISCHARGE_MAX_ERROR;
    } else {
        warnThresh = CURRENT_CHARGE_MAX_WARN;
        errThresh = CURRENT_CHARGE_MAX_ERROR;
    }
    
    if (hallReading > warnThresh) {
        ret |= CURRENT_HIGH | WARN_BIT;
        
        if (hallReading > errThresh)
            ret |= ERROR_BIT;
    }
    
    return ret;
}

/*
 *  hallDischarge
 *
 *  Return:
 *  1 if the hall sensor measures positive current, 0 otherwise
 *
 */
int1 hallDischarge(void) {
    return (hallSensor.data > 0);
}

//Retrieves and returns uint16 raw voltage or temperature value from sensor
uint16 getRawSensorVal(uint8 sensorNum, uint8 sensorRegister) {
    uint8 loBits, hiBits;
    sensorNum<<=1;
    
    // Read most significant byte, contains bits 3-9
    i2c_start();
    i2c_write(sensorNum + I2C_WRITE_BIT);
    i2c_write(sensorRegister);
    i2c_start();
    i2c_write(sensorNum + I2C_READ_BIT);
    hiBits = i2c_read(0);
    i2c_stop();
    
    // Read least significant byte, contains bits 0-2
    i2c_start();
    i2c_write(sensorNum + I2C_WRITE_BIT);
    i2c_write(sensorRegister + 1);
    i2c_start();
    i2c_write(sensorNum + I2C_READ_BIT);
    loBits = i2c_read(0);
    i2c_stop();
    
    return(combineBytes(hiBits,loBits));
}

//Retrieves and returns uint16 raw current value from hall effect sensor
uint16 getRawCurrentVal(void) {
    uint16 rawCurrent;
    rawCurrent = read_adc();
    
    return(rawCurrent);
}

//Combines the two bytes (uint8) received from sensor into one (uint16)
uint16 combineBytes(uint8 high, uint8 low) {
    /* Quick bit masking sanity check to make sure we're never returning ints
       greater than 2^10 */
    uint16 top = ((uint16)high << 3) & 0x03F8;
    uint16 bot = ((uint16)low >> 5) & 0x0007;
    
    return (top + bot);
}

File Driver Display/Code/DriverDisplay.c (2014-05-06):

/** Driver display code for spitfire
    main() runs setup for adc, timers, CAN, and pwm
    loops to check potentiometer for intended brightness
    checks CAN line for motor controller, mppt, and BPS data
    converts raw values from CAN and potentiometer to output values
    write output values to LED controllers
*/

#include <18F26K80.h>
#device adc = 8

#FUSES NOWDT                    //No Watch Dog Timer
#FUSES NOXINST                  //Extended set extension and Indexed Addressing mode disabled (Legacy mode)
#FUSES LP                       //Low power osc < 200 khz
#FUSES BROWNOUT
#FUSES HSH                      //High speed Osc, high power 16MHz-25MHz
#FUSES NOPLLEN                  //4X HW PLL disabled, 4X PLL enabled in software
#FUSES SOSC_DIG                 //Digital mode, I/O port functionality of RC0 and RC1
#FUSES PUT
#FUSES NOIESO
#FUSES NOFCMEN
#FUSES NOPROTECT

#use delay(clock=20000000)
#use SPI(MASTER, CLK=PIN_C3, DI=PIN_C5, DO=PIN_C4, MODE=0, BITS=8, STREAM=SPI_1, MSB_FIRST)

#define LED PIN_C0
#define RTS PIN_C5
#define LE PIN_C0   // Latch Enable
#define OE PIN_C1   // Output Enable
#define BUZZER PIN_C2

#define MOTOR_CONT_ID 0x400
#define BUS_ID        MOTOR_CONT_ID + 2
#define VELOCITY_ID   MOTOR_CONT_ID + 3

#define MPPT_ID       0x600

#define BPS_ID        0x800
#define BPS_ERROR     BPS_ID + 5

// Modified CAN library includes default FIFO mode, timing settings match MPPT, 
// and 11-bit instead of 24-bit addressing
#include "../../Shared/Code/can-18F4580_mscp.c"

typedef unsigned int8 uint8;
typedef unsigned int16 uint16;

void setup(void);
int getCANData(void);
void translateRawValues(void);
void writeLeftBar(int8 powerInput);
void writeRightBar(int8 powerOutput);
void writesevenSegment(int16 carSpeed);

// Driver LED bytes
int barL[] = {0x00,0x01,0x03,0x07,0x0F,0x1F,0x3F,0x7F,0xFF};
int barR[] = {0x00,0x80,0xC0,0xE0,0xF0,0xF8,0xFC,0xFE,0xFF};
int segment[] = {0xEE,0x82,0xDC,0xD6,0xB2,0x76,0x7E,0xC2,0xFE,0xF6}; // 0-9
int segChar[] = {0x2C,0xEE,0xBA,0x82}; //L, O, H, I

//Raw data
int8 potentiometer;
int8 busCurrent[4];
int8 busVoltage[4];
int8 motorRPM[4];
int8 mpptCurrent[2];
int8 mpptVoltage[2];
int8 BPSData[6];

//Real values
int8 brightness;
int8 inputPower;
int8 outputPower;
int16 sevenSegment;
int1 BPSWarn[4]
int16 miscLights;

/**uint8 leftBar = 0, rightBar = 0;
int8 misc[4] = {1, 0, 1, 1};
uint8 segmentNum = 0;*/

void setup(void) {
    //adc setup
    setup_adc(ADC_CLOCK_DIV_32);
    setup_adc_ports(sAN10|VSS_VDD);
    set_adc_channel(10);
    delay_us(10);
    
    //timer setup
    setup_timer_4(T4_DISABLED,0,1);
    setup_comparator(NC_NC_NC_NC);// This device COMP currently not supported by the PICWizard
    setup_spi(SPI_MASTER|SPI_SCK_IDLE_LOW|SPI_XMIT_L_TO_H|SPI_CLK_DIV_16|SPI_SAMPLE_AT_MIDDLE);
    
    //CANBus setup
    can_init();
    set_tris_b((*0xF93 & 0xFB) | 0x08); //b3 is out, b2 is in (default)
    
    //PWM setup
    //output_low(OE);
    //output_low(LE);
    //setup_ccp2(OE); //Configure CCP2 as a PWM 
    //setup_power_pwm_pins(PWM_OFF, PWM_ON, PWM_OFF, PWM_OFF);
}

void main() {
    setup();
    
    while(1){
        output_high(RTS);       
        potentiometer = read_adc(); //potentiometer is 8bit [0,255]

        output_low(OE);
        output_low(LE);
        //set_pwm2_duty(potentiometer%100);
        //if (getCANData())
        //    writeDisplay(mpptIn, motorOut, BPSWarn, (int)carSpeed);
        
        //leftBar = //MPPT input;
        rightBar = outputPower % 8;
        writeDisplay(leftBar,rightBar,misc,segmentNum);
        segmentNum = ++segmentNum%10;
   }
}

int getCANData(void) {
    struct rx_stat rxstat;
    int32 rx_id;
    int8 in_data[8];
    int rx_len;
    
    // If there is no CAN message waiting in the queue, return
    if !(can_kbhit())
        return 0;
    
    // If data is waiting in buffer...
    if(can_getd(rx_id, in_data, rx_len, rxstat)) {
        switch(rx_id) {
        case BUS_ID:
            memcpy(busCurrent, &in_data[0], 4);
            memcpy(busVoltage, &in_data[4], 4);            
            break;            
        case VELOCITY_ID:
            memcpy(motorRPM, &in_data[4], 4);
            break;
        case MPPT_ID:
            memcpy(mpptCurrent, &in_data[0], 2);
            memcpy(mpptVoltage, &in_data[2], 2);
            break;
        case BPS_ERROR:
            memcpy(BPSData, in_data, 6);
            break;
        }
    }   
    return 1;
}

void translateRawValues(void) {
   float busCurr = IEEEToPICFloat(busCurrent);
   float busVolt = IEEEToPICFloat(busVoltage);
   outputPower = (int8)busCurr * (int8)busVolt;
   //translate outputPower/8
   
   motorRPM = IEEEToPICFloat(&in_data[4]);
   carSpeed = (int8)motorRPM * 50;
   //translate carSpeed to sevenSegment
   
   float mpptCurr = IEEEToPICFloat(mpptCurrent);
   float mpptVolt = IEEEToPICFloat(mpptVoltage);
   inputPower = (int8)mpptCurr * (int8)mpptVolt;
   //translate inputPower/8
   
   BPSWarn[0] = BPSData[0] | BPSData[1]&0xFC;  // Over Voltage
   BPSWarn[1] = BPSData[2] | BPSData[3]&0xFC;  // Under Voltage
   BPSWarn[2] = BPSData[4] | BPSData[5]&0xFC;  // Over Temperature
   BPSWarn[3] = BPSData[5]&0x01;               // Over Current
   //translate BPSWarn to Misc Lights
}

float IEEEToPICFloat(unsigned int8 *rawValues) {
    unsigned int8 temp[4];
    float f;

    int1 sign =  bit_test(rawValues[3], 7);
    int1 lsb = bit_test(rawValues[2], 7);
    
    temp[0] = IEEEraw[3];
    temp[1] = IEEEraw[2];
    temp[2] = IEEEraw[1];
    temp[3] = IEEEraw[0];

    temp[0] = (raw[0] << 1) | lsb;
    temp[1] = (raw[1]&0x7F) | (sign << 7);
    
    // Load raw binary
    memcpy(&f, &temp, 4);

    return f;
}
/*  writeDisplay()
 *
 *  barL       - number between 0 and 8 inclusive
 *  barR       - number between 0 and 8 inclusive
 *  bottomLEDs - four misc lights on bottom
 *  num        - number to be displayed on the 7+1 segment display
 */
void writeDisplay(uint8 lBarN, uint8 rBarN, int8 bottomLEDs[4], signed int8 num) {
    uint8 lSeg;
    uint8 rSeg;
    int8 bot = 0;
    bot |= ((bottomLEDs[0]&1) << 7);
    bot |= ((bottomLEDs[1]&1) << 6);
    bot |= ((bottomLEDs[2]&1) << 1);
    bot |=  (bottomLEDs[3]&1);
    
    if (num < 0) {
        lSeg = segChar[0];      // L
        rSeg = segChar[1];      // O
    } else if (num > 99) {
        lSeg = segChar[2];      // H
        rSeg = segChar[3];      // I
    } else {
        lSeg = segment[num / 10];
        rSeg = segment[num % 10];
    }

    
    spi_write(bot);                 // 2 Bottom Left LEDs
    spi_write(barL[lBarN]);         // Left Bar
    spi_write(barR[rBarN]);         // Right Bar
    spi_write(bot);                 // 2 Bottom Right LEDs
    spi_write(swapNibble(rSeg));    // Right Seg
    spi_write(lSeg);                // Left Seg
    
    // Enable latch momentarily then disable, why?
    output_high(LE);
    delay_ms(1);
    output_low(LE);
}
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

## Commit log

2013-11-26 Changed pretty much nothing, but added the manual
    LED is turning on and off, but any changes are stopping the LED and
    nothing is coming from the serial port output
2013-11-26 Changed printc to printf
2013-11-26 Closing Commit for the Semester
    Still results in wrong output
    [VoltageSensorTest.c]
2014-01-10 Previous problems fixed
    Lun (who is refusing to use git) fixed the file!
    [VoltageSensorTest.c]
2014-01-16 ALL NEW ALL FREE INFO ON HALL EFFECT SENSORS
    [Blue Hall Effect Sensor FW Bell CL-50.xlsx]
2014-01-17 Added hall effect board calibration
2014-01-18 Added calibration data
    Added in libreoffice format so its crossplatform
    [CL-50 Board calibration.ods]
2014-01-21 Add calibration docs
2014-01-21 Added CANbus library header
    because lun forgot it
2014-01-27 Real initial commit
    [Battery Protection Board.brd, Battery Protection Board.sch]
2014-01-30 Add more things/Orginization
    [Battery Protection Board.brd, Battery Protection Board.sch, Blue Hall Effect Sensor FW Bell CL-50.xlsx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]
2014-01-31 CANBus send/receive now working
2014-02-07 fixed paul's broken code
    [BatteryProtectionSystem.c]
2014-02-11 Finally fixed the for loop error
    The problem was we were indexing rawVoltageData with an 8bit int instead
    of a 16bit int, this was causing casting problems since rawVoltageData
    is an array of uint16.
    Also fixed formatting in other files and removed commented out line in
    can_init()
    [BatteryProtectionSystem.c]
2014-02-26 More sensor monitoring code.
    Sensor data is now stored in a struct with the sensor ID, temp and
    voltage reading, as well as the temperature and voltage error counters
    [BatteryProtectionSystem.c]
2014-03-05 cosmetic changes, added relay text code, fixed code in setPacketFunction
    [BatteryProtectionSystem.c]
2014-03-18 Added circuitry
    [Blue Hall Effect Sensor FW Bell CL-50.xlsx, CAN-USB_adapter.brd, CAN-USB_adapter.sch]
2014-03-18 Added stuff
    [Battery Protection Board.brd, Battery Protection Board.sch, CAN-USB_adapter.brd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]
2014-03-18 real telem_board_v6
    previous one was v5
    [telem_board.sch]
2014-03-18 Renamed the Schematics folder
    its almost 9
    [Battery Protection Board.brd, Battery Protection Board.sch, CAN-USB_adapter.brd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]
2014-03-18 Set up folders for merge
    [Blue Hall Effect Sensor FW Bell CL-50.xlsx, CL-50 Board calibration.ods]
2014-03-18 Paul told me
    [Battery Protection Board.brd, Battery Protection Board.sch, CAN-USB_adapter.brd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]
2014-03-20 Removed redundant circuitry folder in telem
    [telem_board.brd]
2014-03-20 "Added driver display code"
    -Quote by Paul Correira
2014-03-20 Started updating driver display
2014-03-20 Removed schematics from code file
    [radio_interface.sch, telem_board.sch, temp_sensor.sch]
2014-03-24 Driver display documentation/organization
2014-03-26 Changed BPS Protocol
    Documentation only though, Lun changed the code. Also added the
    temperature sensor data sheet
2014-03-27 Added telemetry MOTOR CONT and BPS receive code
2014-03-27 Added eagle files for sensor configuration
    Code soon
    [SensorConfiguration.brd, SensorConfiguration.sch]
2014-03-27 Added sensor config code
2014-03-28 Created new Driver display code file
2014-03-28 Deleted old driver display
2014-03-28 Moved CAN and LCD libraries to shared folder
    Added docs for the issues with floating point numbers
    [BatteryProtectionSystem.c, DriverDisplay.c, TelemetryReceive.c]
2014-03-29 Fixed memcpy syntax, added float utils
    memcpy syntax should be (DST, SRC, N), not src, dst.
    [DriverDisplay.c, TelemetryReceive.c]
2014-04-01 driver display docs
2014-04-15 Add Driver Control stuff
2014-04-23 Added LED datasheets
2014-04-23 Driver display changes
2014-05-02 Revert "added things"
    This reverts commit 3bedffcbdf7fcd56a5a3bfa4455c198752032db1.
    [18F26K80.h]
2014-05-02 added devices 18f26k80.h
2014-05-06 Added Components Library
    used to be named eagle-6.2.0/lbr/MSCP_2011_v2.lbr
    I also added a component for a 2x1 led.
    It is also on Dropbox, but I'm trying to use GitHub more, since it is
    simpler
2014-05-06 Changed driver display
